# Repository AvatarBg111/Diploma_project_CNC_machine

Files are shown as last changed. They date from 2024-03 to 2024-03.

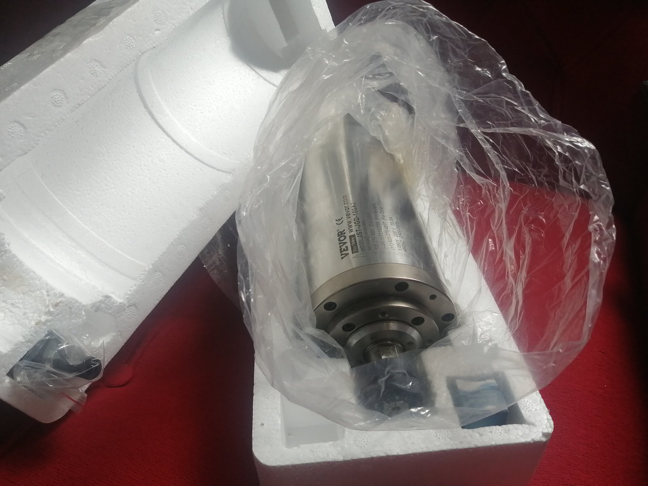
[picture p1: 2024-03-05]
Docs/Pictures/spindle_2.jpg

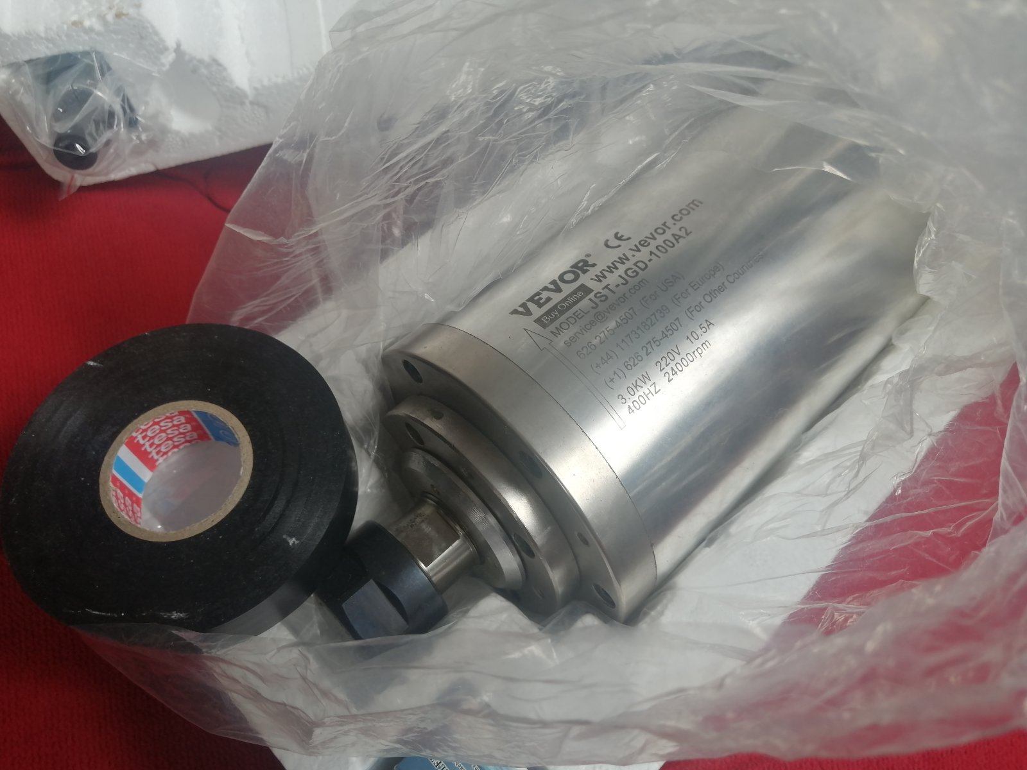
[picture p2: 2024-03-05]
Docs/Pictures/spindle_1.jpg

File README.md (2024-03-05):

# Diploma_project_CNC_machine
Repository for diploma project on the topic "System for controlling a CNC machine"

## V0.1 - 23.01.2024
 - most peripherals are configured
 - made loading screen with main menu
 - working on functionality of main and sub menus
 - working on MPG (manual pulse generator) mode

## V0.2 - 09.02.2024
 - Most menus/submenus are partially functional
 - MPG settings (for axes and spindle) are to be implemented
 - MPG mode is partially functional

## V0.3 - 19.02.2024
 - Main functionalities are complete

## V1.0 - 05.03.2024
 - Basic documentation added

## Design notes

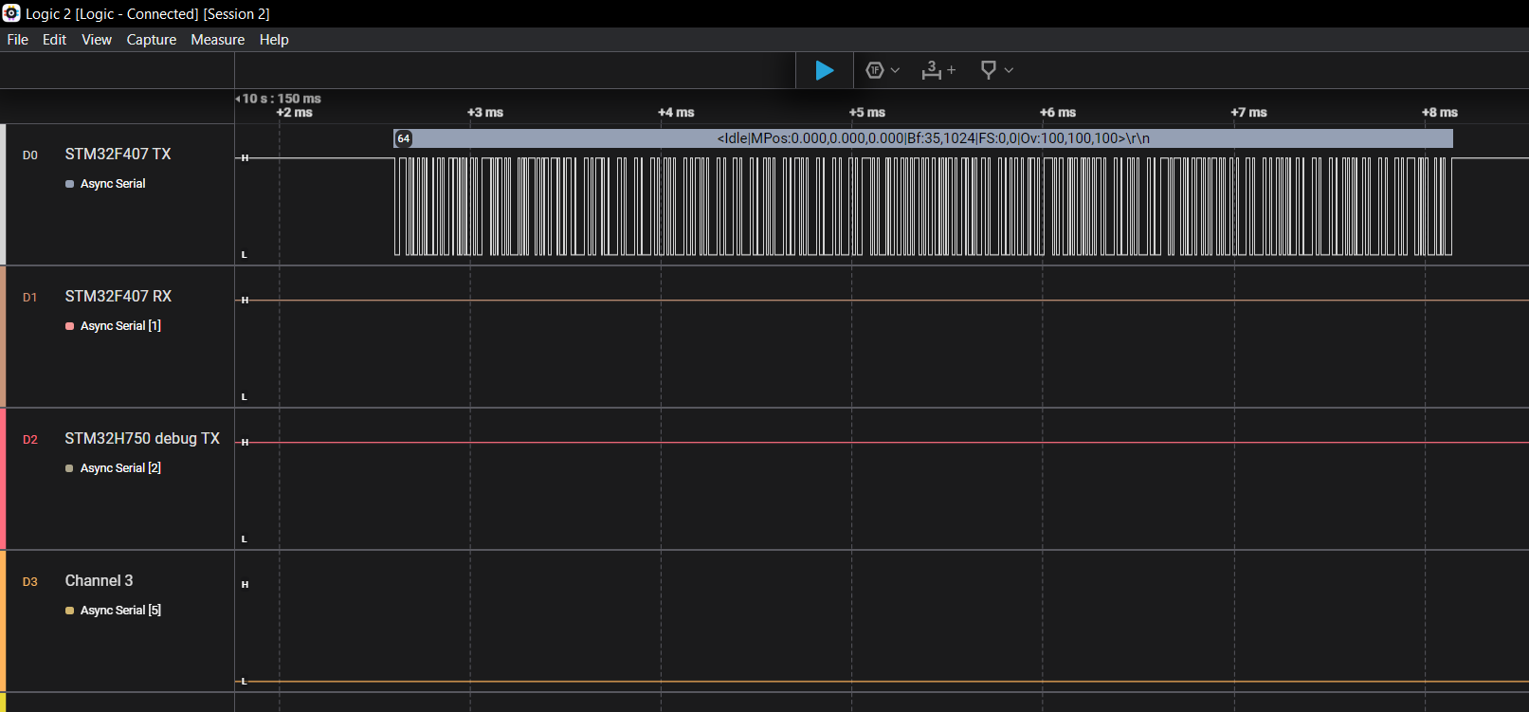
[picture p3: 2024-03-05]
Docs/Captures/grblHAL_MPG_communication_saleae_capture_6.png

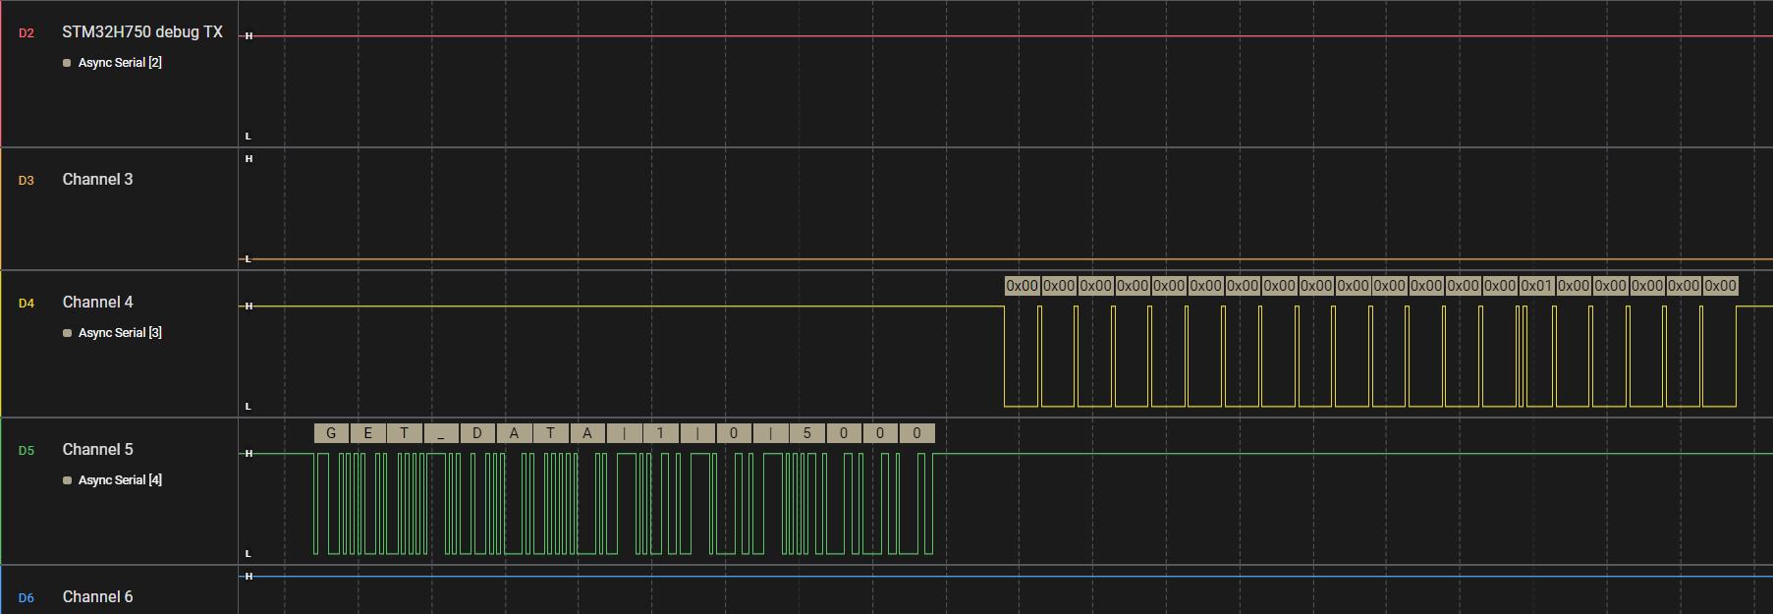
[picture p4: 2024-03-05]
Docs/Captures/pendant_communication_saleae_capture_1.png

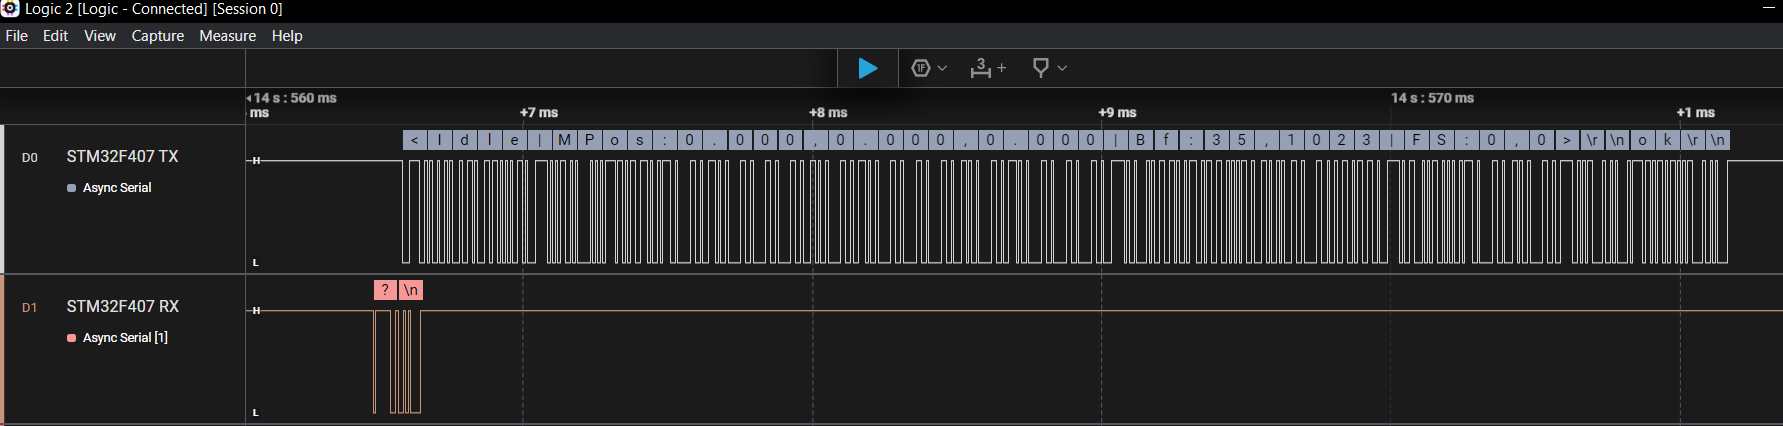
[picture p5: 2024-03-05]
Docs/Captures/grblHAL_MPG_communication_saleae_capture_1.png

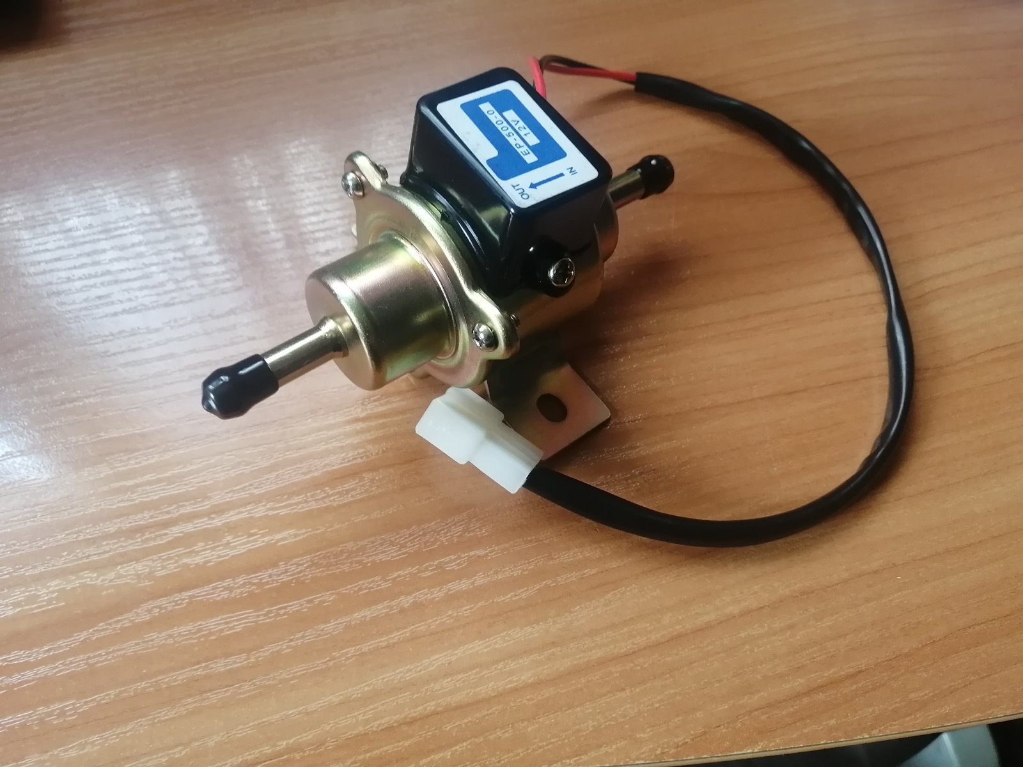
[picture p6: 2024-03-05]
Docs/Pictures/oil_pump.jpg

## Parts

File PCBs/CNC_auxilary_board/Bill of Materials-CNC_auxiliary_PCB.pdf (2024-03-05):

Value | Designator | Footprint | Quantity | Comment | Description
470μF | C1, C2, C3, C4 | CAP 8x12 | 4 | 470μF | Electrolytic capacitor, Long Life 8000h/105C, Low impedance, 470uF/ 16V 20%, 8.0x11.5mm, RM3.5mm
100nF 50V | C5, C6, C7, C8, C11, C12, C13, C15, C16, C17, C18 | SMD 0603 CAP | 11 | 100nF 50V | 100nF 50V X7R +-10%
22uF 16V | C9 | SMD 1206 CAP | 1 | 22uF 16V | 22uF 16V X5R +-20%
220μF | C10, C14 | CAP 6.3x12 | 2 | 220μF | Electrolytic capacitor, RM series, 20%,-40~105°C, 6.3x7mm RM2.5
1N4148W | D1, D2, D3, D5, D6, D7, D9, D10, D12, D13, D14, D17 | SOD123 | 12 | 1N4148W | Diode Standard 100V 300mA _DC_ Surface Mount SOD-123
SK24 | D4 | SMB | 1 | SK24 | Diode 40V 2A UFM0.55V/2A IFM 50A IR 0.45mA, Schottky
KP-2012SURCK | D8 | SMD 0805 LED-R | 1 | KP-2012SURCK | LED 2.0x1.25mm, 50-160 mcd@20mA, W.Clear, 120°
BZV55C6V8 | D11, D16 | SOD80C | 2 | BZV55C6V8 | 500 mW 5% 6.8V minimelf
BZV55C22 | D15 | SOD80C | 1 | BZV55C22 | 500 mW 5% 22V minimelf
5A | F1, F3 | FUSE HOLDER | 2 | 5A | Fuse Holder, 250 V, 6 A, Pcb Fuse Holder, Through Hole, P22,4mm
10A | F2 | FUSE HOLDER | 1 | 10A | Fuse Holder, 250 V, 6 A, Pcb Fuse Holder, Through Hole, P22,4mm
Wire | J1, J2, J3, J4, J5, J6, J7, J8, J11, J12, J13, J14, J15, J16, J17, J18, J19, J20, J21, J22, J23, J24, J27, J28, J30, J31 | Wire-2 | 26 | +12V, Water pump +, GND, Water pump -, +12V_OUT, Oil pump +, Oil pump -, +48V X, +48V X OUT, button STOP, +48V Y, +48V Y OUT, +48V Z, +48V Z OUT, Coil A+, Coil B+, Coil A-, Coil B-, High Voltage A-, High Voltage B-, Water sensor, Oil sensor | Wire
PN1X7 | J9 | PN1X7 | 1 | PN1X7 | Single Row / Straight / Without Shroud Female header Female 7 | WÃ¼rth Elektronik 61300711821 @ Pin header, socket _Si...
PN1X8 | J10 | PN1X8 | 1 | PN1X8 | Single Row / Straight / Without Shroud Female header Female 8 | WÃ¼rth Elektronik 61300711821 @ Pin header, socket _Si...
PN1X2 | J25, J26, J29, J32, J33, J34, J35 | PN1X2 | 7 | X limit switch, Y limit switch, Z limit switch, Probe switch, Hold button, Start button, Door switch | Single Row / Straight / Without Shroud Female header Female 2@ Pin header, socket _Si...
RAS-12-15 | K1, K2, K3, K4, K5, K6, K7 | RELAY RAS-12-15 (SPDT) | 7 | RAS-12-15 | RELAY 12V /30mA 15A/ 24VDC(120VAC) 10A/ 250VAC
CL220uH | L1, L2 | INDC RBQE | 2 | CL220uH | Toroidal Coil 220uH 0.099 ohm 3000mA 20%
CL1.0mH | L3 | DRH104R | 1 | CL1.0mH | CL1.0mH SDI104R (DRH104R); 2.959 ohm, 0.48A, 20%
DTC114YKA | Q1, Q3, Q5, Q6, Q9, Q13, Q18, Q20, Q21, Q22, Q23, Q25, Q27, Q28, Q29, Q30 | SOT-346 (SC59) Black | 16 | DTC114YKA | NPN Digital 50V 100mA 200mW R1=10kOm R2=47kOm
AP2306GN | Q2, Q4, Q7, Q10, Q11, Q14, Q15, Q16 | SOT-23-3 | 8 | AP2306GN | NMOS 20V 5.3A 1.38W 35mOhm/4.5V; 50mOhm/2.5V
SST2222A | Q8, Q12, Q19, Q26 | SOT-23-3 | 4 | SST2222A | Transistor NPN 40V 600mA 300MHz 350mW
BC807-25 | Q17, Q24 | SOT-23-3 | 2 | BC807-25 | Transistor PNP 45V 500mA 0.25W HFE 160-400
22k | R1, R3, R4, R6, R8, R9, R11, R12, R14, R16, R17, R18, R19, R20, R22, R23, R29, R30, R31, R33, R34, R37, R38, R39, R41, R42 | SMD 0603 | 26 | 22k | RES
47k | R2, R5, R10, R15, R21, R24, R26, R28 | SMD 0603 | 8 | 47k | RES
10k | R7 | SMD 0603 | 1 | 10k | RES
2,4k | R13, R27, R36 | SMD 0603 | 3 | 2,4k | RES
220k | R25, R35 | SMD 0603 | 2 | 220k | RES
15k | R32, R40 | SMD 0603 | 2 | 15k | RES
SMBJ13A | TZ1 | DO-214AA (SMB) | 1 | SMBJ13A | Transient Voltage Suppressors, Uni-directional, 600W, UBRmin14.4V@1mA

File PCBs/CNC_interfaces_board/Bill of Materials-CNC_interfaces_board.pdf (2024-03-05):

Value | Designator | Footprint | Quantity | Comment | Description
680μF | C1 | CAP 10x16 | 1 | 680μF | Electrolytic capacitor, TM series, 20%,-55~105°C, 10x16mm RM5, 0.1Ohm
10uF | C2 | SMD 1210 CAP | 1 | 10uF | C1210 10uF 35V X7R
220uF | C3 | SMD 7343-43 | 1 | 220uF | Cap Tant Solid 220uF 10V E CASE 10% _7.3 X 4.3 X 4mm_ SMD 7343-43 0.1 Ohm 125В °C T/R
100nF 50V | C4 | SMD 0603 CAP | 1 | 100nF 50V | 100nF 50V X7R +-10%
100uF | C5 | SMD 1210 CAP | 1 | 100uF | 100uF 10V X5R +-20%
1N4148W-7-F | D1, D2, D3 | SOD123 | 3 | 1N4148W-7-F | Diode Standard 100V 300mA _DC_ Surface Mount SOD-123
KP-2012 | D4, D5, D6, D7 | SMD 0805 LED-Y | 4 | KP-2012 WHITE, KP-2012 GREEN, KP-2012 ORANGE, KP-2012 RED | LED 2.0x1.25mm, 50-160 mcd@20mA, W.Clear, 120°
LQH32CN471K23L | FB1 | SMD 1210 LQH | 1 | LQH32CN471K23L | 470uH 19Ohm 60mA 10% 47uH 1.3Ohm 170mA 10%
Wire | J1, J2 | Wire-2 | 2 | +12V, GND | Wire
FPC-40PinConnector | J3 | 687140149022 | 1 | FPC-40PinConnector | 40 Position FFC, FPC Connector Contacts, Bottom 0.020 (0.50mm) Surface Mount, Right Angle
PN1X8 | J4, J8, J10, J11 | PN1X8 | 4 | PN1X8 | Single Row / Straight / Without Shroud Female header Female 8 | WÃ¼rth Elektronik 61300711821 @ Pin header, socket _Si...
PN1X4 | J5, J9 | PN1X4 | 2 | PN1X4 | Single Row / Straight / Without Shroud Female header Female 4 @ Pin header, socket _Si...
PN1X7 | J6 | PN1X7 | 1 | PN1X7 | Single Row / Straight / Without Shroud Female header Female 7 | WÃ¼rth Elektronik 61300711821 @ Pin header, socket _Si...
FPC-6PinConnector | J7 | 687106149022 | 1 | FPC-6PinConnector | 6 Position FFC, FPC Connector Contacts, Bottom 0.020 (0.50mm) Surface Mount, Right Angle
Buzzer | LS1 | XDCR_KSSG13J12-N | 1 | Buzzer
LTV356T | OPT1, OPT2 | MINI-FLAT-4 | 2 | LTV356T | Optoisolator Transistor Output 3750Vrms 1 Channel 4-SOP
DTC114YKA | Q1, Q4, Q5, Q6, Q7, Q8, Q9, Q10, Q11, Q12, Q13, Q14, Q15, Q16, Q17, Q18, Q19, Q20, Q21, Q22, Q24 | SOT-346 (SC59) Black | 21 | DTC114YKA | NPN Digital 50V 100mA 200mW R1=10kOm R2=47kOm
SST2222A | Q2, Q3, Q23 | SOT-23-3 | 3 | SST2222A | Transistor NPN 40V 600mA 300MHz 350mW
10k | R1, R2, R3, R4, R5, R6, R7, R8, R9, R10, R11, R12, R13, R14, R21, R24, R26, R27, R29, R31, R33, R35, R37, R39, R40, R41, R42, R43, R44, R45, R46, R47, R48, R49, R50, R51 | SMD 0805 | 36 | 10k | RES
220Ohm | R15, R16, R17, R18 | SMD 0805 | 4 | 220Ohm | RES
2,7k | R19, R20, R22, R23, R25, R28, R30, R32, R34, R36, R38 | SMD 0805 | 11 | 2,7k | RES
1k | R52 | SMD 0805 | 1 | 1k | RES
Button | SW1, SW2, SW3, SW4, SW5, SW6 | SW_KSR221GLFS | 6 | Button | Tactile Switch 2p SPST-NO 50mA/32V 6x3.8x2.5mm
STM32H750VBT6 WeActStudio | U1 | WeActStudio STM32H750VBT6 | 1 | STM32H750VBT6 WeActStudio | Board
STM32F407VGT6 DevEBox | U2 | DevEBox V3.0 STM32F407VGT6 | 1 | STM32F407VGT6 DevEBox | Board
BA05CC0WFP-E2 | U3 | DPAK228P968X238-4N | 1 | BA05CC0WFP-E2 | LDO Regulator

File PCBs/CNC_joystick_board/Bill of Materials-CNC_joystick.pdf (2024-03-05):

Value | Designator | Footprint | Quantity | Comment | Description
470μF | C1 | CAP 8x12 | 1 | 470μF
22uF | C2 | YelloW SMD 1210 CAP TANT | 1 | =+'22uF'+' '+'16V' | TANT B SMD 22uF 16V 293D226X9016B2TE3
100nF 50V | C3, C5, C6, C7, C8, C9, C10 | SMD 0603 CAP | 7 | 100nF 50V | CL10B104KB85PNC
10uF | C4 | Yellow SMD 1206 CAP TANT | 1 | =+'10uF'+' '+'10V' | TANT A SMD 10uF 10V TAJA106K010RNJ
ZLLS1000TA | D1 | SOT-23-3 | 1 | ZLLS1000TA | Schottky Diode, Vr=40V, If=1.16A, Uf=0.43V/1.0A, Ifsm=22A/<100us, Ir=5uA typ, trr=5.0ns typ
OSY5LU3133A | D2, D3, D4, D5, D6, D7 | LED-3mm Y | 6 | OSY5LU3133A | LED 3mm, 80mcd@20mA, 590nm Yellow, Transparent, 30°
OSR6NU3134A | D8, D9, D10, D11 | LED-3mm R | 4 | OSR6NU3134A | 3mm, 20mcd@30mA, 640nm Hi-Eff Red, Diffused, 30°
MF-NSMF035X-2 | F1 | SMD 1206 FUSE | 1 | MF-NSMF035X-2 | PTC Resettable Fuse, Ihold 0.35A, 16V, SMD 1206
Wire | J1, J2, J3, J4 | PN1X4, Wire-2 | 4 | PN1X4, p1, p2 | Single Row / Straight / Without Shroud Female header Female 4 @ Pin header, socket _Si..., Wire
CL1.0mH | L1 | DRH104R | 1 | CL1.0mH | CL1.0mH SDI104R (DRH104R); 2.959 ohm, 0.48A, 20%
1k | R1, R4 | SMD 0603 | 2 | 1k | RES
100k | R2, R3 | SMD 0603 | 2 | 100k | RES
270R | R5, R6, R7, R8, R9, R10, R11, R12, R18, R19 | SMD 0603 | 10 | 270R | RES
180R | R13, R14, R15, R16, R17 | SMD 0603 | 5 | 180R | RES
encoder | SW1, SW2 | PN1X4 | 2 | encoder | Handwheel CNC Pulser, Rotary Encoder, 60mm, 100PPR, 5V, 4Pin, <=120mAq Silver
Switch 3 Pos | SW3, SW4, SW11, SW12 | PN1X8 | 4 | Switch 3 Pos | Latching, 22mm, 5V, 8Pin, Silver, Blue led
Switch 2 Pos | SW5 | PN1X4 | 1 | Switch 2 Pos | Latching, 16mm, 5V, 3Pin, Silver
Button 1 LED | SW6, SW7, SW8, SW9, SW10 | PN1X4 | 5 | Button 1 LED | Momentary, 22mm, 5V, 4Pin, Silver, Led
SMBJ13A | TZ1 | DO-214AA (SMB) | 1 | SMBJ13A | Transient Voltage Suppressors, Uni-directional, 600W, UBRmin14.4V@1mA
MCP1703T-3302E | U1 | SOT-89(MB) | 1 | MCP1703T-3302E | 3.3V±2% 250mA, LDO 0.725V, Vinmax=16V, linear voltage regulator
STM32F103C8T6 | U2 | QFP50P900X900X160-48N | 1 | STM32F103C8T6 | ARMÂ® CortexÂ®-M3 STM32F1 Microcontroller IC 32-Bit 72MHz 64KB (64K x 8) FLASH 48-LQFP (7x7)

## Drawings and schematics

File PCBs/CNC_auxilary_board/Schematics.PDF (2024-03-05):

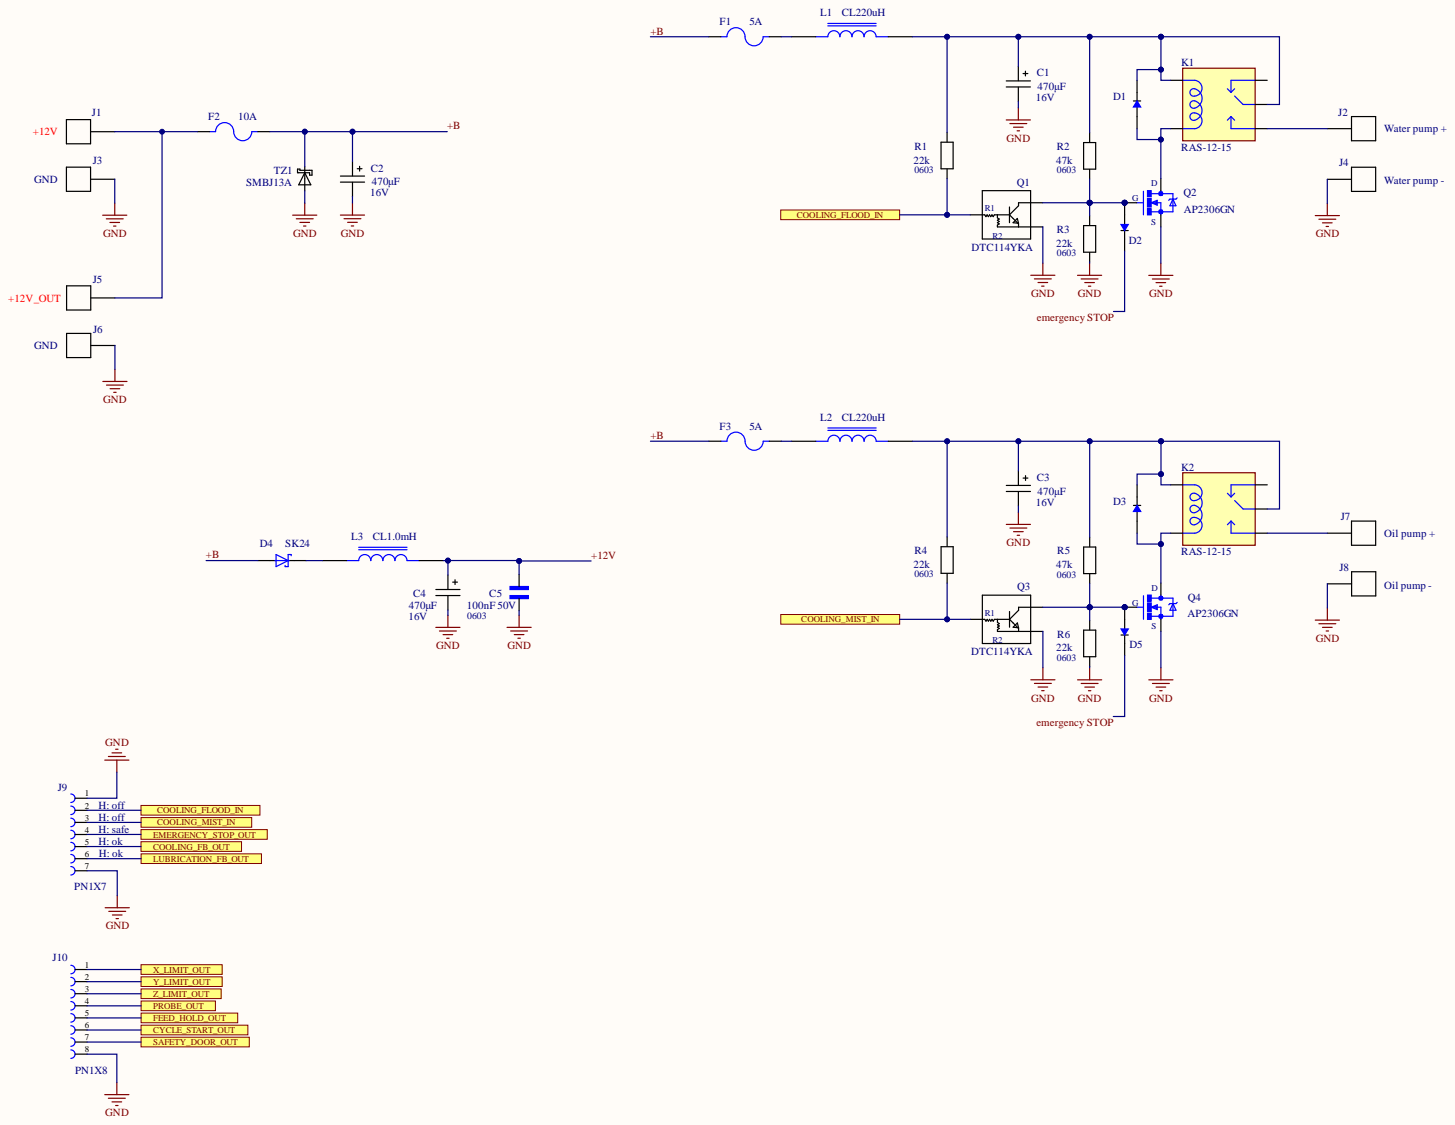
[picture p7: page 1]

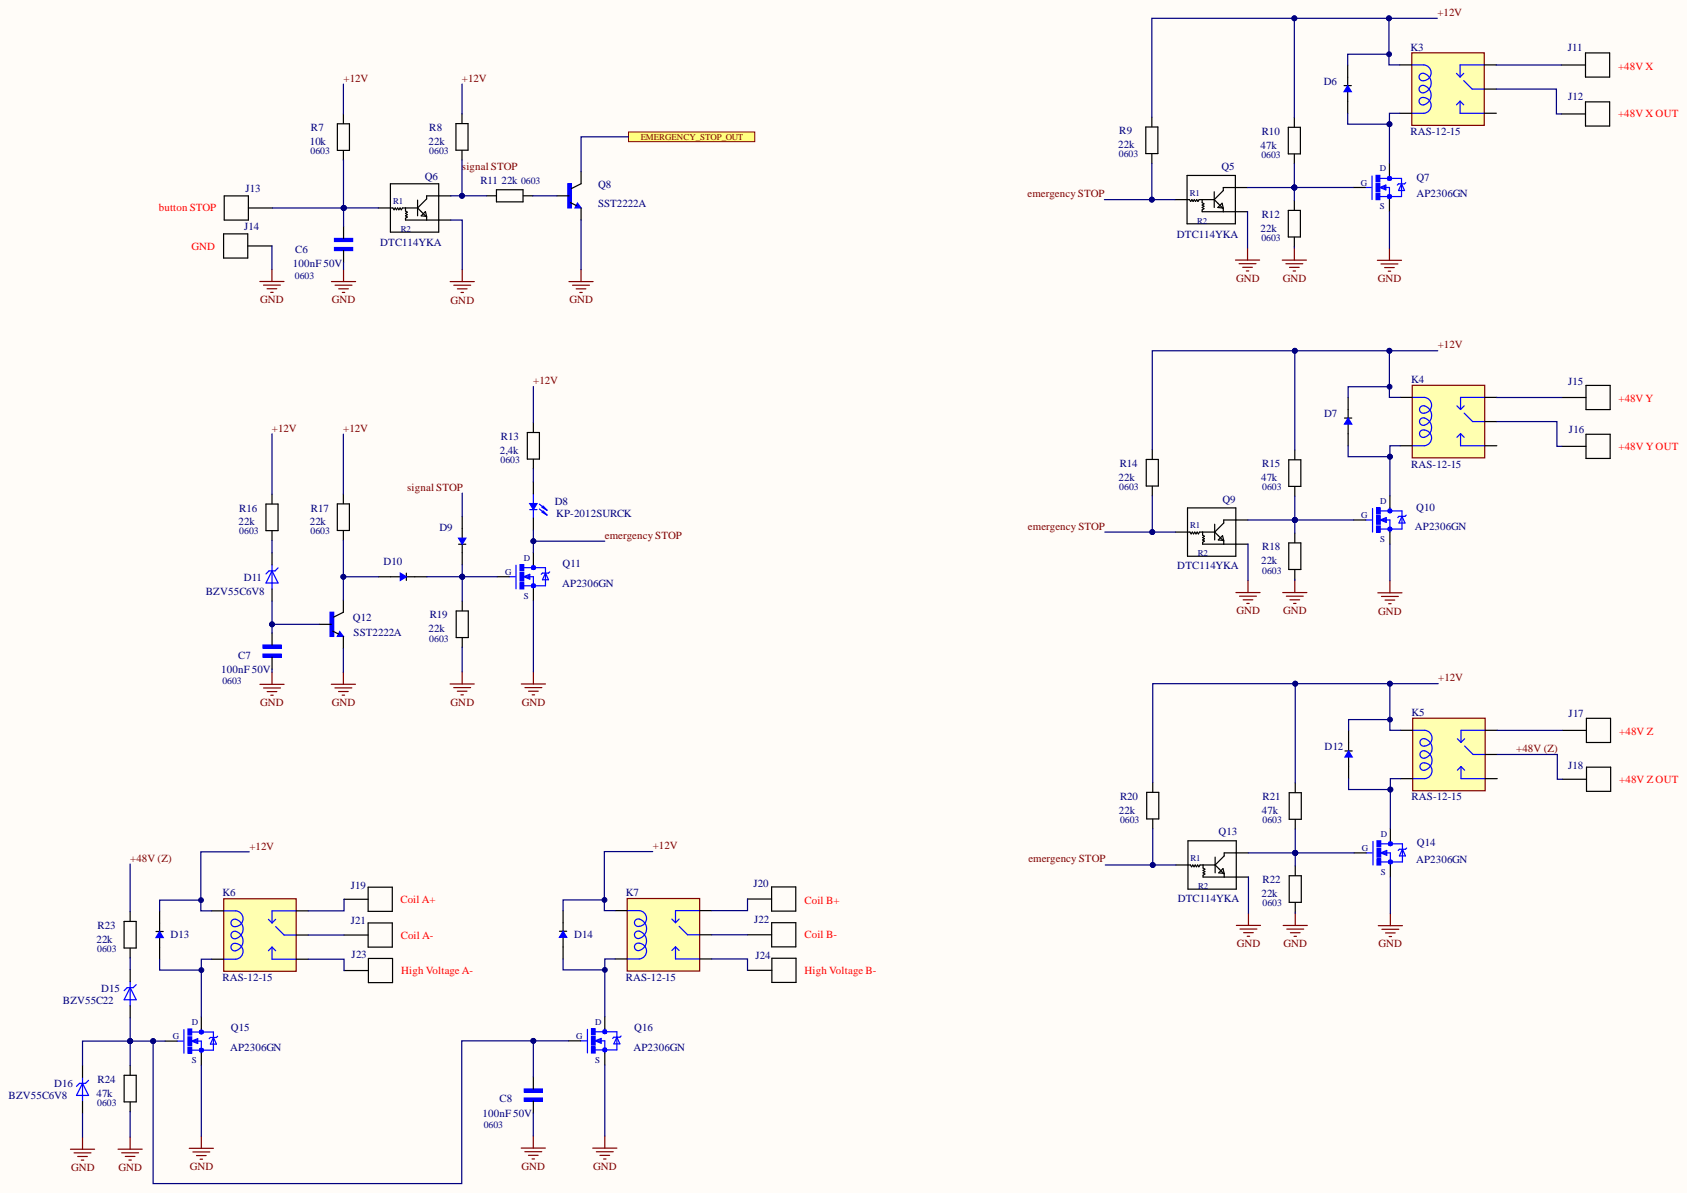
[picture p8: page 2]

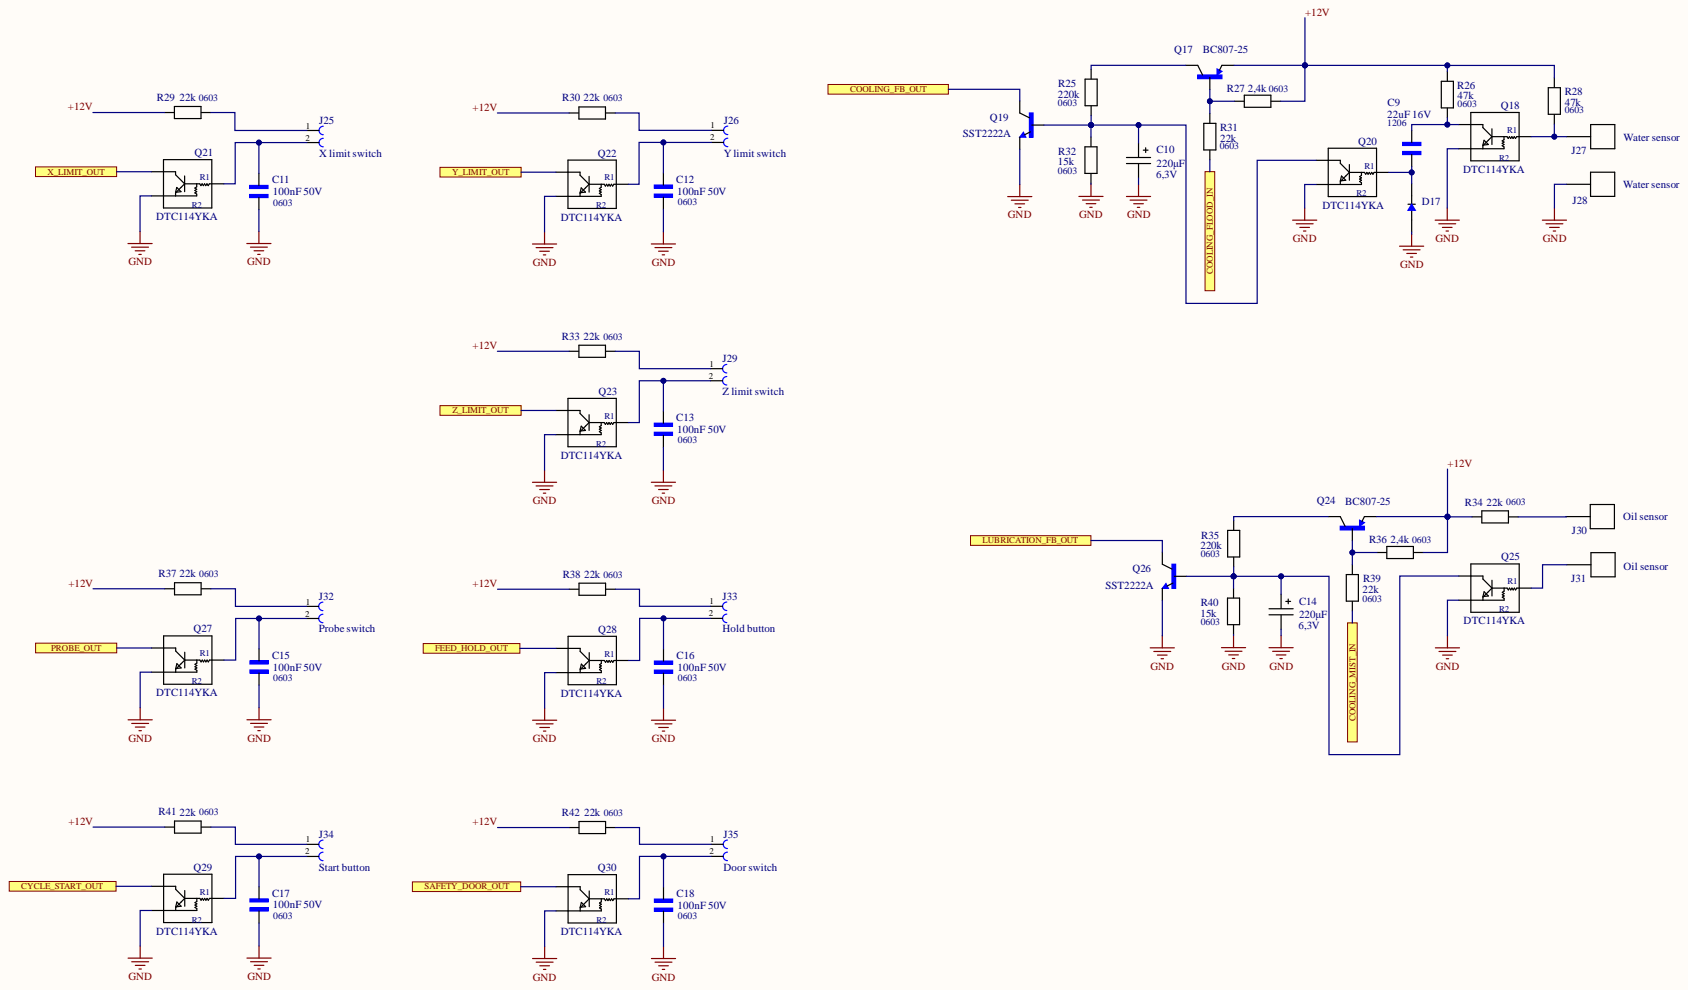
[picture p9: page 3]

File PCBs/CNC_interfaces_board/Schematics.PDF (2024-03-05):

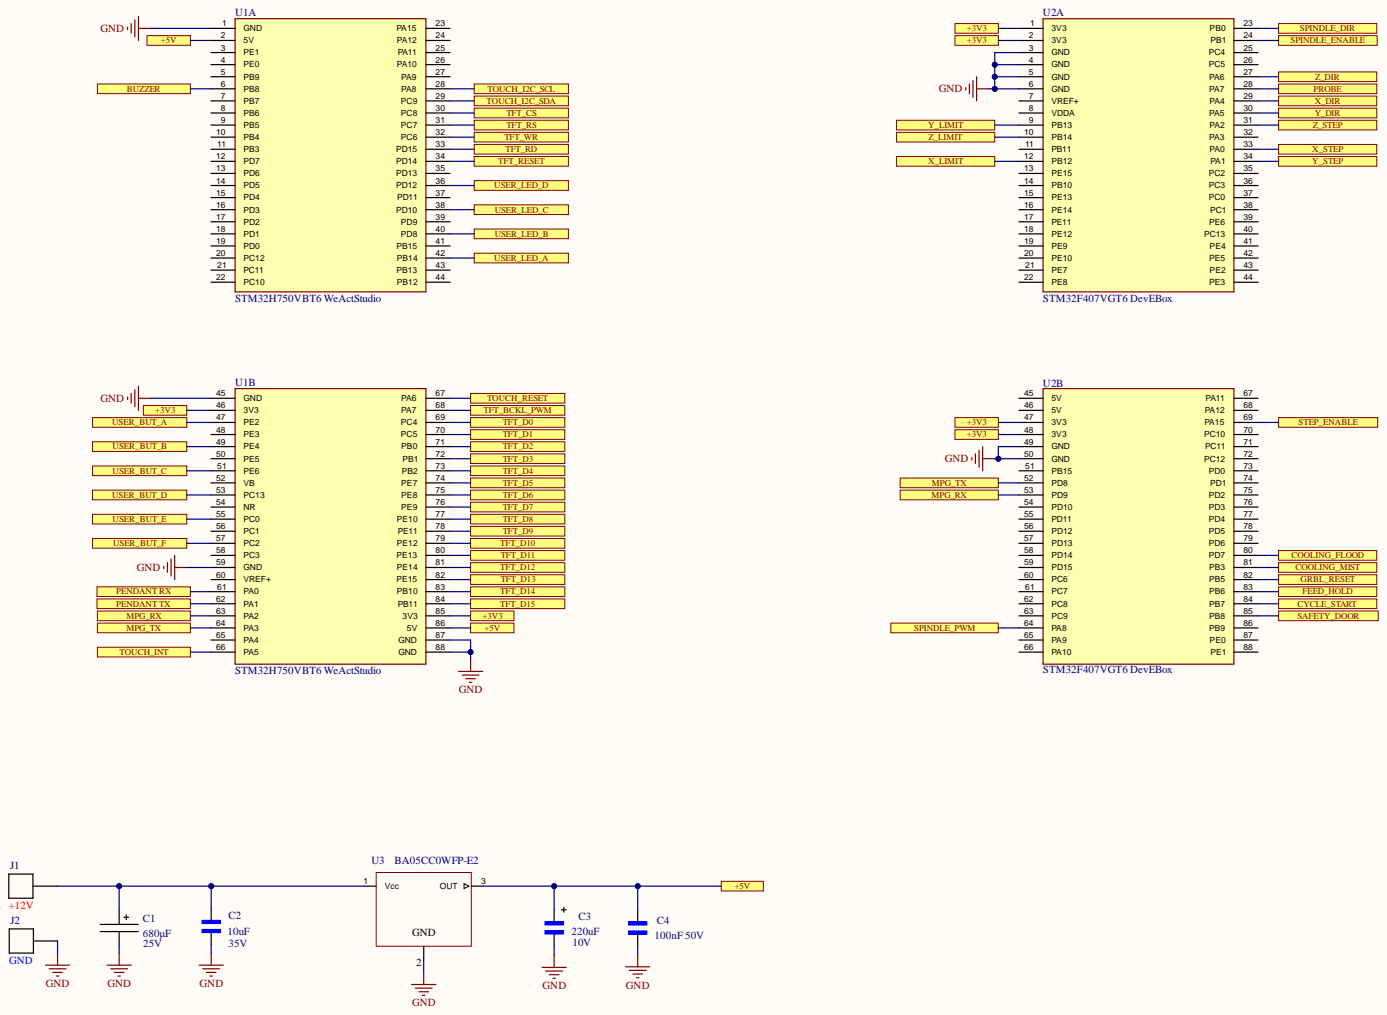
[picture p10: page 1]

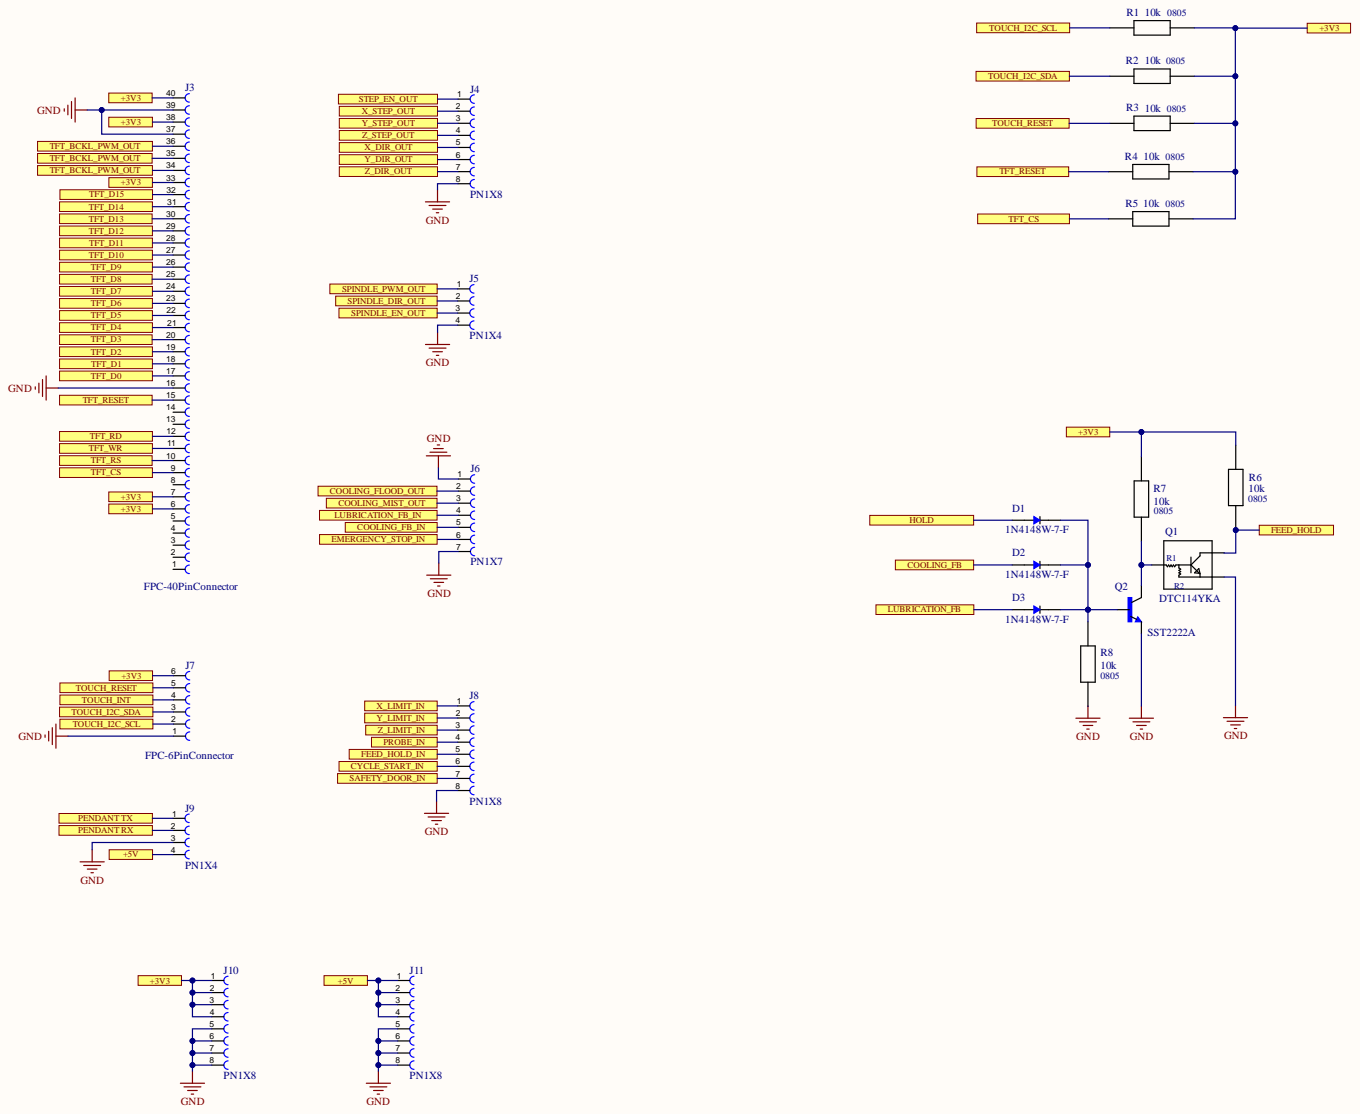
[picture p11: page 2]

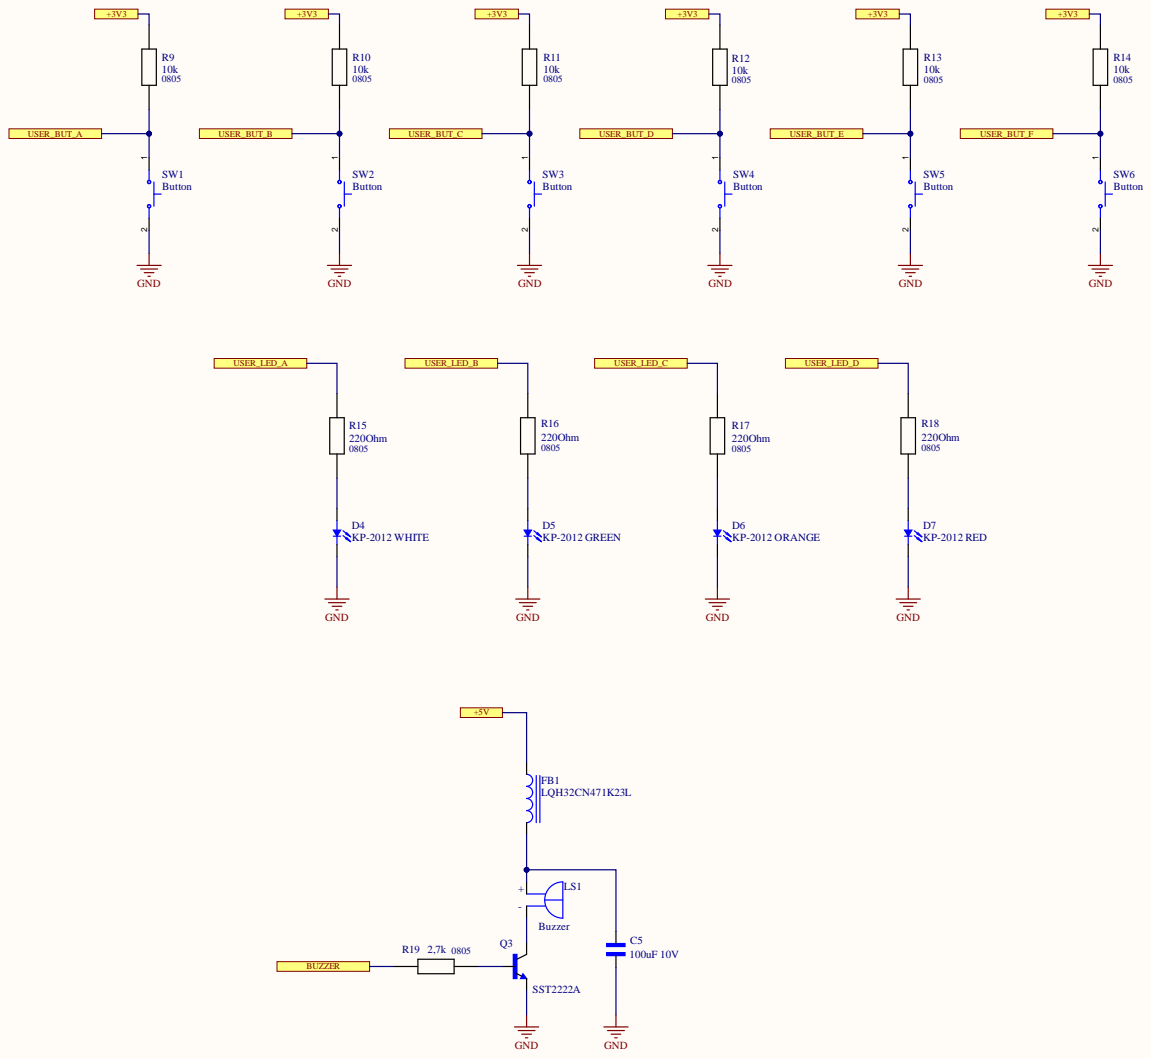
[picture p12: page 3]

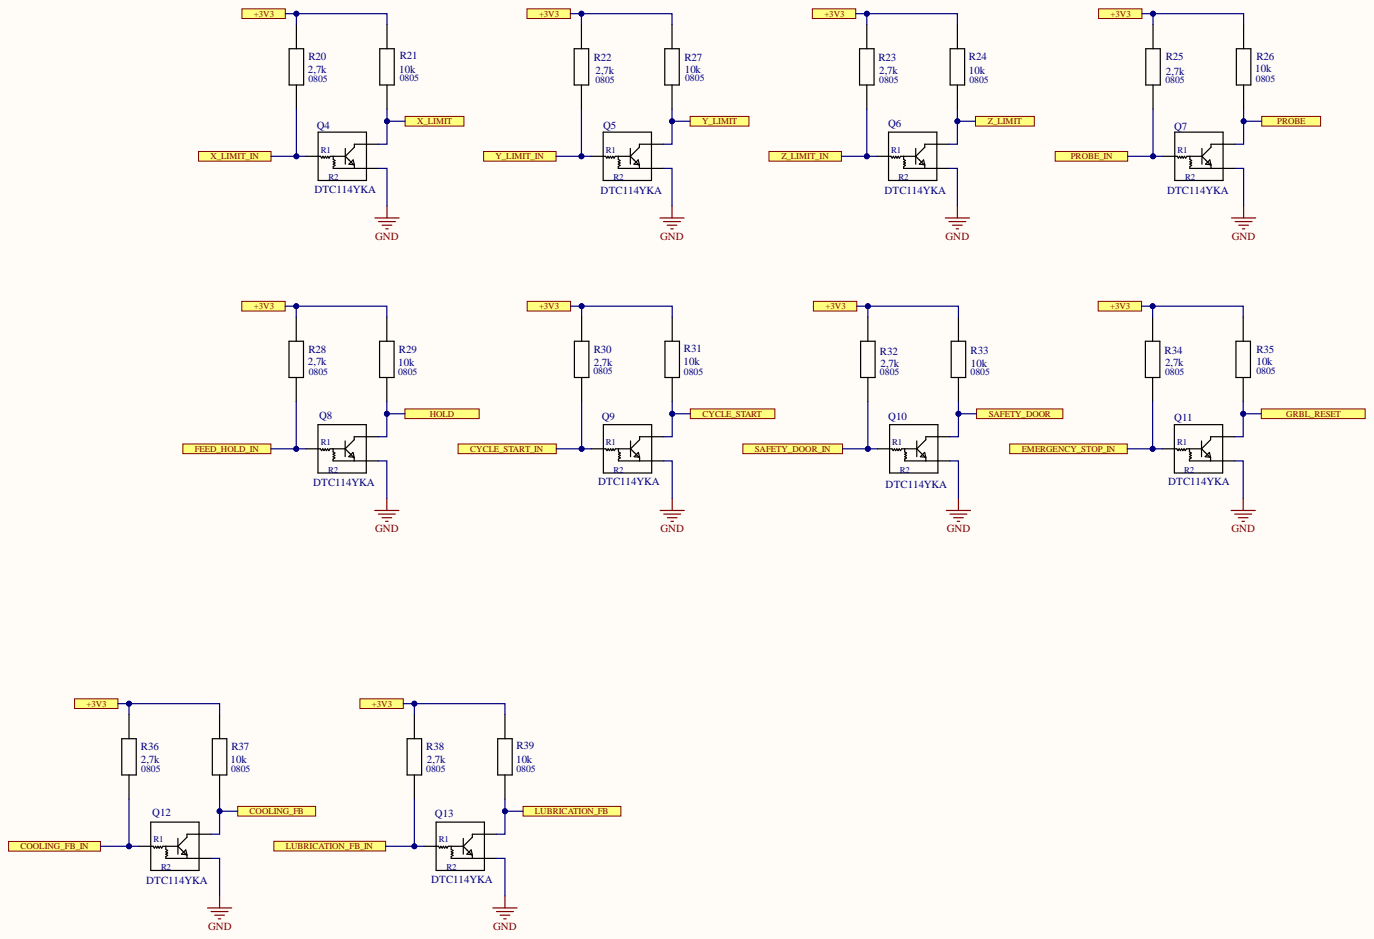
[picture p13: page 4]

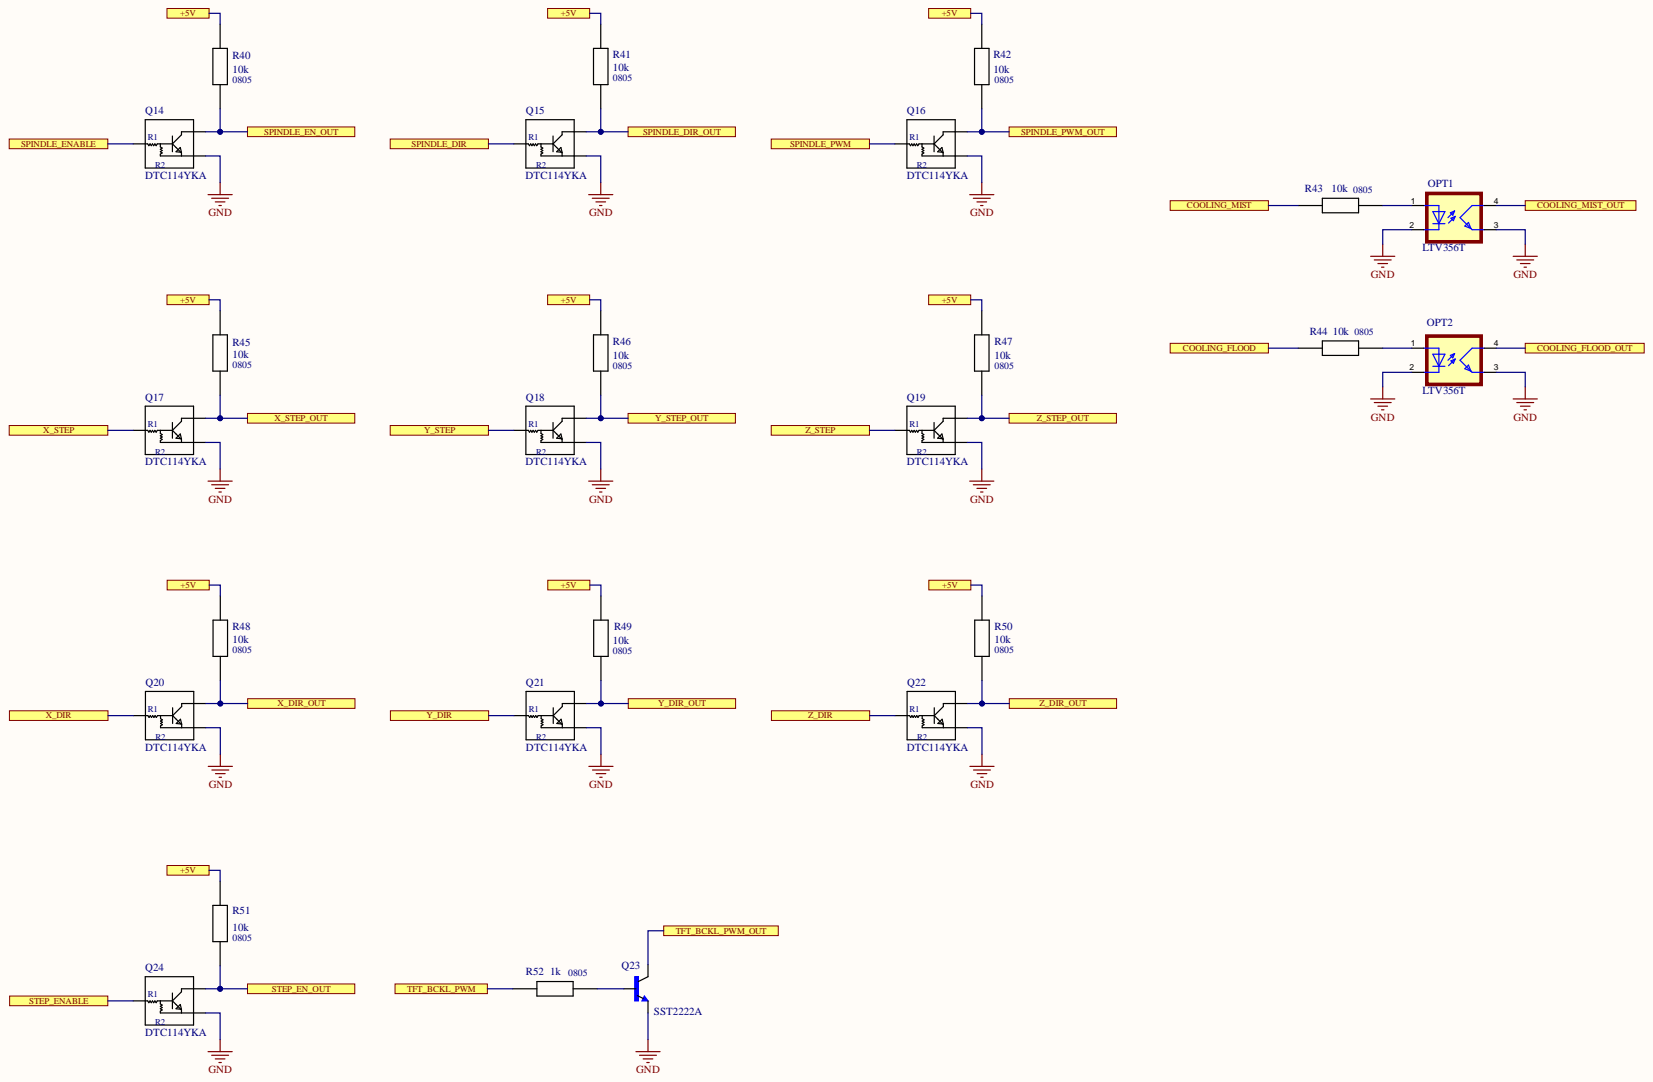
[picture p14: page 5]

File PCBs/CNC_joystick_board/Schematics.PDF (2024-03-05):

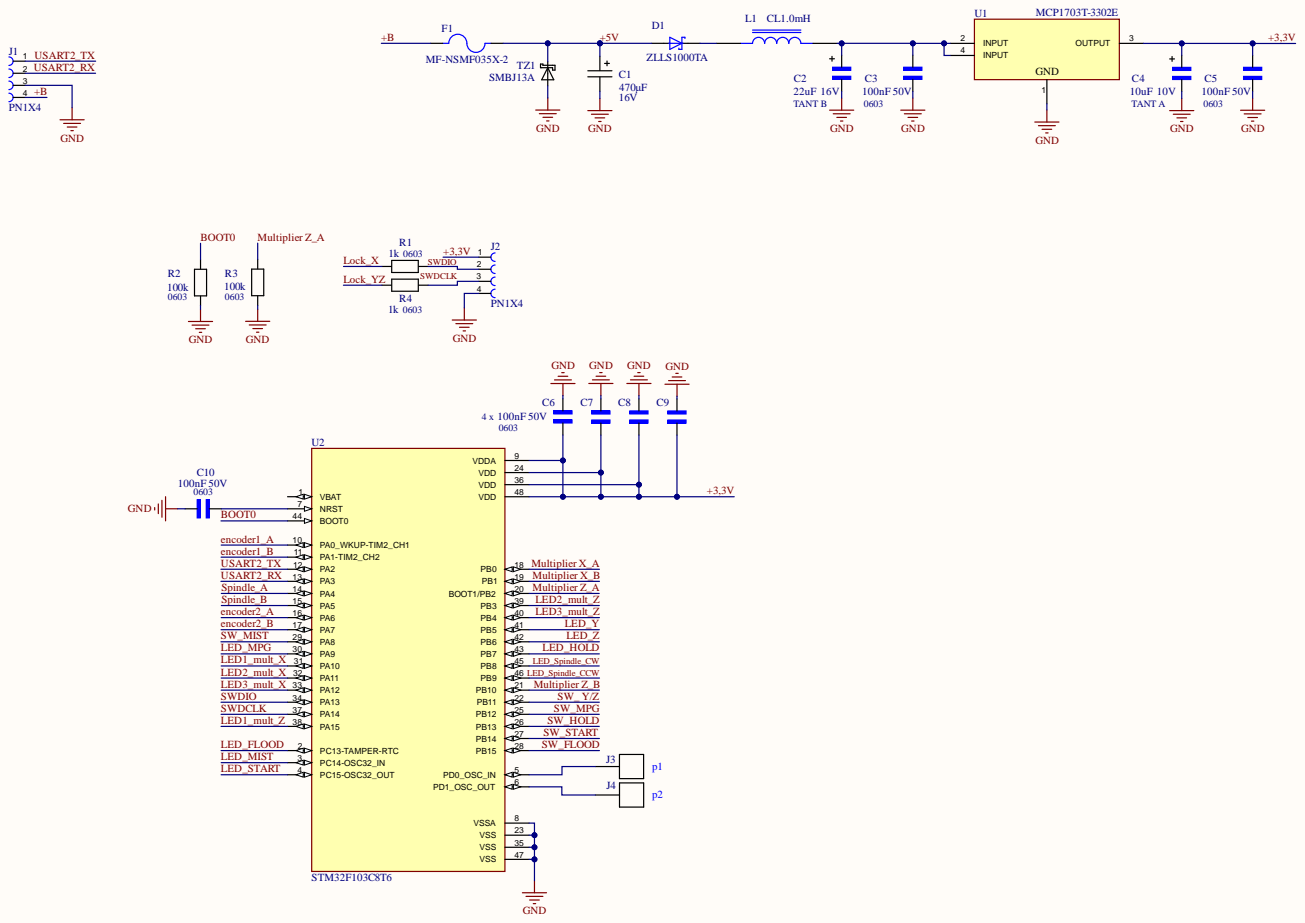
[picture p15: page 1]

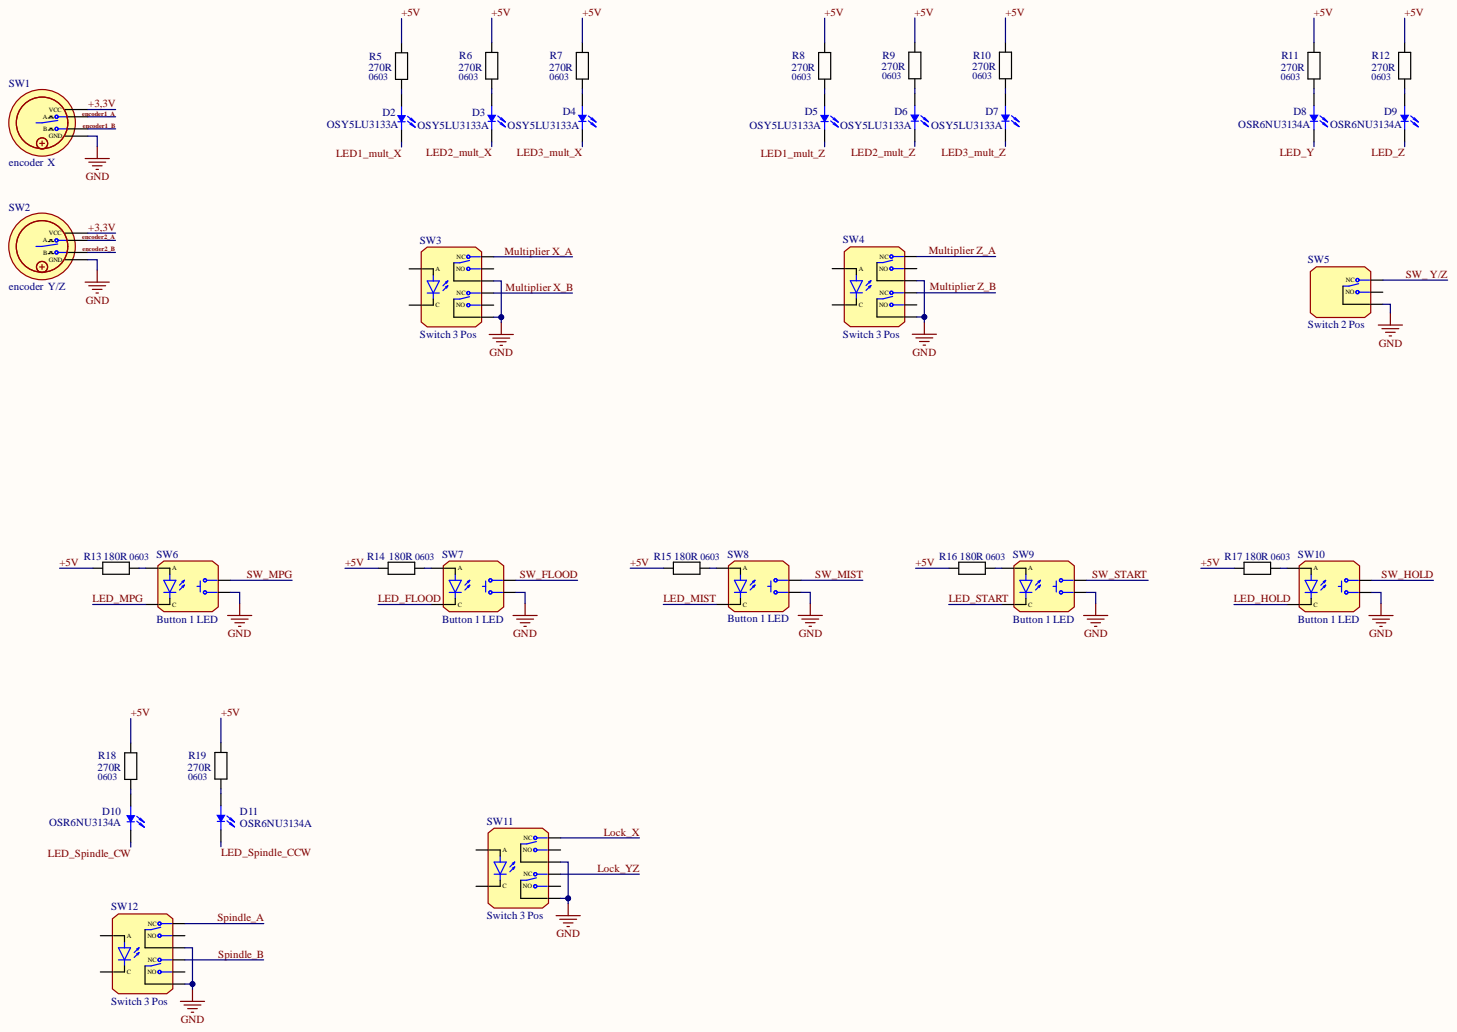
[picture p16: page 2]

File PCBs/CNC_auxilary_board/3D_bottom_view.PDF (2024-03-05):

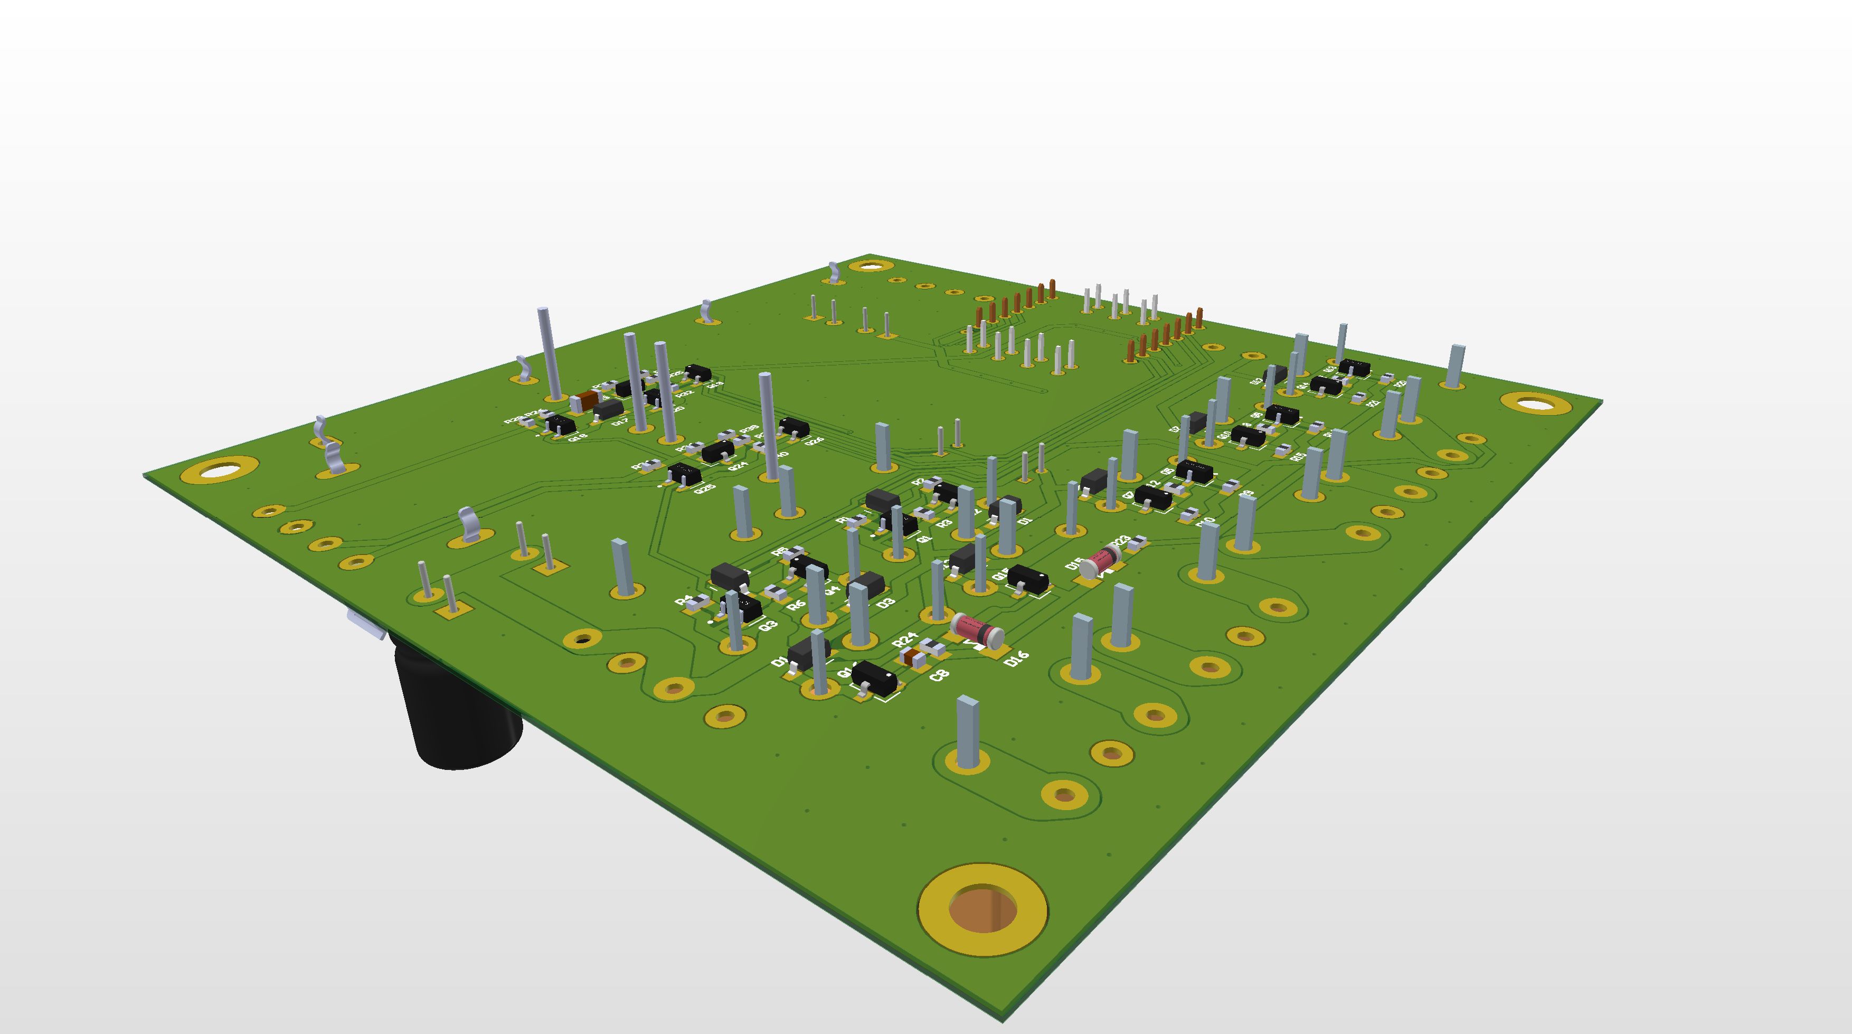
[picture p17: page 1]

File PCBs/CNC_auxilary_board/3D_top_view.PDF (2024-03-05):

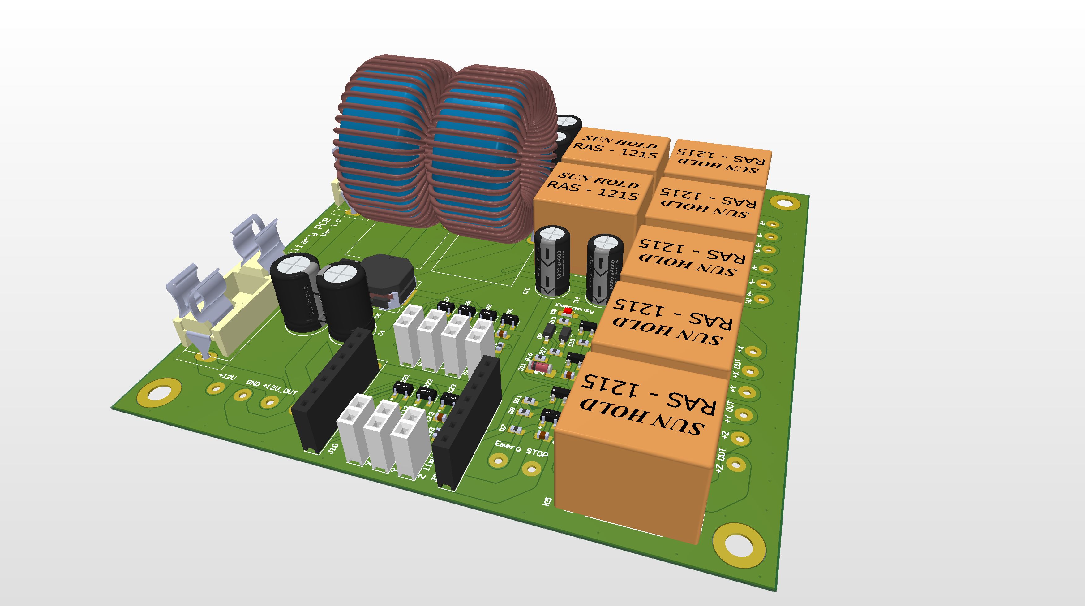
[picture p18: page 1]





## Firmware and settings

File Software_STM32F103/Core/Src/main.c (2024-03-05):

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
/* Includes ------------------------------------------------------------------*/
#include "main.h"

/* USER CODE BEGIN Includes */
#include "buttons.h"
#include "uart_comm.h"
#include "stm32f1xx_it.h"

/* USER CODE END Includes */

/* USER CODE BEGIN PD */
#define Y_OR_Z_BUT_DELAY_CH 0
#define MPG_BUT_DELAY_CH 1
#define FLOOD_BUT_DELAY_CH 2
#define MIST_BUT_DELAY_CH 3

/* USER CODE END PD */

TIM_HandleTypeDef htim2;
TIM_HandleTypeDef htim3;
TIM_HandleTypeDef htim4;

UART_HandleTypeDef huart2;
DMA_HandleTypeDef hdma_usart2_rx;
DMA_HandleTypeDef hdma_usart2_tx;

/* USER CODE BEGIN PV */
bool process_inputs_flag = false;
bool pendant_status = false;
uint8_t pendant_mpg_status = MPG_STATUS_DISABLED;

uint8_t button_action_delay_cnt_ch[16] = {0};
const uint8_t button_delay_action_cnt = BUTTON_DELAY_ACTION_TIME / PROCESS_INPUTS_DELAY;

/* USER CODE END PV */

void SystemClock_Config(void);
static void MX_GPIO_Init(void);
static void MX_DMA_Init(void);
static void MX_TIM2_Init(void);
static void MX_TIM3_Init(void);
static void MX_USART2_UART_Init(void);
static void MX_TIM4_Init(void);
/* USER CODE BEGIN PFP */
void Init_interfaces(void);
void turn_off_leds(void);
void process_inputs(void);
uint8_t get_spindle_mode(void);
uint8_t get_x_axis_multiplier(void);
uint8_t get_yz_axis_multiplier(void);

/* USER CODE END PFP */

/* USER CODE BEGIN 0 */
#define ENCODER_1_TIM htim2
#define ENCODER_2_TIM htim3

extern pendant_data_t pendant_data;

/* USER CODE END 0 */

/**
  * @brief  The application entry point.
  * @retval int
  */
int main(void)
{
  /* MCU Configuration--------------------------------------------------------*/

  /* Reset of all peripherals, Initializes the Flash interface and the Systick. */
  HAL_Init();

  /* Configure the system clock */
  SystemClock_Config();

  /* Initialize all configured peripherals */
  MX_GPIO_Init();
  MX_DMA_Init();
  MX_TIM2_Init();
  MX_TIM3_Init();
  MX_USART2_UART_Init();
  MX_TIM4_Init();
  /* USER CODE BEGIN 2 */
  // Initialize interfaces
  Init_interfaces();

  /* USER CODE END 2 */

  /* Infinite loop */
  /* USER CODE BEGIN WHILE */
  while(1)
  {
	// The program will enter this if statement when the flag
	// has been set which happens inside TIM4 interrupt handler
	if(process_inputs_flag && pendant_status){
		// Call function for processing system inputs
		process_inputs();

		// Reset the entry flag
		process_inputs_flag = false;
	}
    /* USER CODE END WHILE */

    /* USER CODE BEGIN 3 */
  }
  /* USER CODE END 3 */
}

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
/* USER CODE BEGIN 4 */
/**
  * @brief Initialize interfaces
  */
void Init_interfaces(void){
	// Start encoder timers
	HAL_TIM_Encoder_Start(&htim2, TIM_CHANNEL_ALL);
	HAL_TIM_Encoder_Start(&htim3, TIM_CHANNEL_ALL);

	// Start TIM4 for button de-bouncer
	HAL_TIM_Base_Start_IT(&htim4);

	// Assign buttons/switches a de-bouncer channel
	set_button_channel(SPINDLE_MODE_SW_NC_1_GPIO_Port, SPINDLE_MODE_SW_NC_1_Pin, SPINDLE_3POS_SW_NC_1_CH);
	set_button_channel(SPINDLE_MODE_SW_NC_2_GPIO_Port, SPINDLE_MODE_SW_NC_2_Pin, SPINDLE_3POS_SW_NC_2_CH);
	set_button_channel(AXIS_X_MULTIPLIER_SW_NC_1_GPIO_Port, AXIS_X_MULTIPLIER_SW_NC_1_Pin, AXIS_X_MULTIPLIER_SW_NC_1_CH);
	set_button_channel(AXIS_X_MULTIPLIER_SW_NC_2_GPIO_Port, AXIS_X_MULTIPLIER_SW_NC_2_Pin, AXIS_X_MULTIPLIER_SW_NC_2_CH);
	set_button_channel(AXIS_YZ_MULTIPLIER_SW_NC_1_GPIO_Port, AXIS_YZ_MULTIPLIER_SW_NC_1_Pin, AXIS_YZ_MULTIPLIER_SW_NC_1_CH);
	set_button_channel(AXIS_YZ_MULTIPLIER_SW_NC_2_GPIO_Port, AXIS_YZ_MULTIPLIER_SW_NC_2_Pin, AXIS_YZ_MULTIPLIER_SW_NC_2_CH);
	set_button_channel(YZ_SW_GPIO_Port, YZ_SW_Pin, YZ_SW_CH);
	set_button_channel(MPG_SW_GPIO_Port, MPG_SW_Pin, MPG_BUT_CH);
	set_button_channel(HOLD_GPIO_Port, HOLD_Pin, HOLD_BUT_CH);
	set_button_channel(CYCLE_START_GPIO_Port, CYCLE_START_Pin, CYCLE_START_BUT_CH);
	set_button_channel(FLOOD_GPIO_Port, FLOOD_Pin, FLOOD_SW_CH);
	set_button_channel(MIST_GPIO_Port, MIST_Pin, MIST_SW_CH);
	set_button_channel(LOCK_X_AXIS_SW_GPIO_Port, LOCK_X_AXIS_SW_Pin, LOCK_X_AXIS_SW_CH);
	set_button_channel(LOCK_YZ_AXIS_SW_GPIO_Port, LOCK_YZ_AXIS_SW_Pin, LOCK_YZ_AXIS_SW_CH);

	// Turn off all LEDs
	turn_off_leds();

	// Start UART2 reception
	start_uart2_reception();
}

/**
  * @brief Turn off all system LEDs
  */
void turn_off_leds(void){
	HAL_GPIO_WritePin(FLOOD_LED_GPIO_Port, FLOOD_LED_Pin, LED_STATE_OFF);
	HAL_GPIO_WritePin(MIST_LED_GPIO_Port, MIST_LED_Pin, LED_STATE_OFF);
	HAL_GPIO_WritePin(CYCLE_START_LED_GPIO_Port, CYCLE_START_LED_Pin, LED_STATE_OFF);
	HAL_GPIO_WritePin(HOLD_LED_GPIO_Port, HOLD_LED_Pin, LED_STATE_OFF);
	HAL_GPIO_WritePin(MPG_ON_LED_GPIO_Port, MPG_ON_LED_Pin, LED_STATE_OFF);
	HAL_GPIO_WritePin(YZ_SW_LED_Y_GPIO_Port, YZ_SW_LED_Y_Pin, LED_STATE_OFF);
	HAL_GPIO_WritePin(YZ_SW_LED_Z_GPIO_Port, YZ_SW_LED_Z_Pin, LED_STATE_OFF);
	HAL_GPIO_WritePin(SPINDLE_CW_LED_GPIO_Port, SPINDLE_CW_LED_Pin, LED_STATE_OFF);
	HAL_GPIO_WritePin(SPINDLE_CCW_LED_GPIO_Port, SPINDLE_CCW_LED_Pin, LED_STATE_OFF);

	HAL_GPIO_WritePin(AXIS_X_MULTIPLIER_LED_1_GPIO_Port, AXIS_X_MULTIPLIER_LED_1_Pin, LED_STATE_OFF);
	HAL_GPIO_WritePin(AXIS_X_MULTIPLIER_LED_2_GPIO_Port, AXIS_X_MULTIPLIER_LED_2_Pin, LED_STATE_OFF);
	HAL_GPIO_WritePin(AXIS_X_MULTIPLIER_LED_3_GPIO_Port, AXIS_X_MULTIPLIER_LED_3_Pin, LED_STATE_OFF);

	HAL_GPIO_WritePin(AXIS_YZ_MULTIPLIER_LED_1_GPIO_Port, AXIS_YZ_MULTIPLIER_LED_1_Pin, LED_STATE_OFF);
	HAL_GPIO_WritePin(AXIS_YZ_MULTIPLIER_LED_2_GPIO_Port, AXIS_YZ_MULTIPLIER_LED_2_Pin, LED_STATE_OFF);
	HAL_GPIO_WritePin(AXIS_YZ_MULTIPLIER_LED_3_GPIO_Port, AXIS_YZ_MULTIPLIER_LED_3_Pin, LED_STATE_OFF);
}


/**
  * @brief Process system inputs
  */
void process_inputs(void){
	static bool y_or_z_last_state = false;
	uint8_t lock_x_axis = get_button_state(LOCK_X_AXIS_SW_CH);	// Get X axis lock state
	uint8_t lock_yz_axis = get_button_state(LOCK_YZ_AXIS_SW_CH); // Get Y/Z axes lock state

	// Check MPG functionality switch input (it disables/enables MPG functionality)
	if(get_button_state(MPG_BUT_CH) == GPIO_PIN_RESET){
		if(++button_action_delay_cnt_ch[MPG_BUT_DELAY_CH] >= button_delay_action_cnt || \
		   button_action_delay_cnt_ch[MPG_BUT_DELAY_CH] == 1){
			if(button_action_delay_cnt_ch[MPG_BUT_DELAY_CH] != 1 && button_delay_action_cnt != 1){
				button_action_delay_cnt_ch[MPG_BUT_DELAY_CH] = 0;
			}

			if(pendant_mpg_status != MPG_STATUS_DISABLED){
				pendant_mpg_status = MPG_STATUS_DISABLED;
			}else{
				pendant_mpg_status = MPG_STATUS_ENABLE_ONGOING;
			}
		}
	}else{
		button_action_delay_cnt_ch[MPG_BUT_DELAY_CH] = 0;
	}

	// The program will enter this if statement, if the system
	// is enabled and it's MPg functionality is turned on
	if(pendant_status && pendant_data.mpg){
		// Keep or "discard" axis movement data based on locks states
		if(lock_x_axis == GPIO_PIN_RESET){
			pendant_data.encoder1_val = ENCODER_1_TIM.Instance->CNT;
		}else{
			ENCODER_1_TIM.Instance->CNT = pendant_data.encoder1_val;
		}
		if(lock_yz_axis == GPIO_PIN_RESET){
			pendant_data.encoder2_val = ENCODER_2_TIM.Instance->CNT;
		}else{
			ENCODER_2_TIM.Instance->CNT = pendant_data.encoder2_val;
		}
	}else{
		// Discard encoder inputs
		pendant_data.encoder1_val = 0;
		pendant_data.encoder2_val = 0;
		ENCODER_1_TIM.Instance->CNT = 0;
		ENCODER_2_TIM.Instance->CNT = 0;
	}

	// If pendant's MPG functionality is enabled,
	// execute the following code inside the if statement
	if(pendant_mpg_status == MPG_STATUS_ENABLED){
		pendant_data.spindle_mode = get_spindle_mode(); // Get spindle mode
		pendant_data.jog_mode = 0;	//TODO: need to have an input for jogging mode switching
		pendant_data.x_axis_multiplicity = get_x_axis_multiplier(); // Get X axis multiplier
		pendant_data.yz_axis_multiplicity = get_yz_axis_multiplier(); // Get Y/Z axes multiplier

		// Check Y/Z axes switch input
		if(get_button_state(YZ_SW_CH) == GPIO_PIN_RESET){
			if(!y_or_z_last_state){
				y_or_z_last_state = true;
				button_action_delay_cnt_ch[Y_OR_Z_BUT_DELAY_CH] = 0;
			}
			if(++button_action_delay_cnt_ch[Y_OR_Z_BUT_DELAY_CH] >= button_delay_action_cnt){
				button_action_delay_cnt_ch[Y_OR_Z_BUT_DELAY_CH] = 0;
				pendant_data.y_or_z = YZ_MOVEMENT_Z;	// Set to Z axis
			}
		}else{
			if(y_or_z_last_state){
				y_or_z_last_state = false;
				button_action_delay_cnt_ch[Y_OR_Z_BUT_DELAY_CH] = 0;
			}
			if(++button_action_delay_cnt_ch[Y_OR_Z_BUT_DELAY_CH] >= button_delay_action_cnt){
				button_action_delay_cnt_ch[Y_OR_Z_BUT_DELAY_CH] = 0;
				pendant_data.y_or_z = YZ_MOVEMENT_Y;	// Set to Z axis
			}
		}

		// Check FLOOD coolant switch input
		if(get_button_state(FLOOD_SW_CH) == GPIO_PIN_RESET){
			if(++button_action_delay_cnt_ch[FLOOD_BUT_DELAY_CH] >= button_delay_action_cnt){
				button_action_delay_cnt_ch[FLOOD_BUT_DELAY_CH] = 0;
				pendant_data.flood = (pendant_data.flood ? false : true);
			}
		}else{
			button_action_delay_cnt_ch[FLOOD_BUT_DELAY_CH] = 0;
		}

		// Check MIST coolant switch input
		if(get_button_state(MIST_SW_CH) == GPIO_PIN_RESET){
			if(++button_action_delay_cnt_ch[MIST_BUT_DELAY_CH] >= button_delay_action_cnt){
				button_action_delay_cnt_ch[MIST_BUT_DELAY_CH] = 0;
				pendant_data.mist = (pendant_data.mist ? false : true);
			}
		}else{
			button_action_delay_cnt_ch[MIST_BUT_DELAY_CH] = 0;
		}

		// Check HOLD and Cycle start button input
		if(get_button_state(HOLD_BUT_CH) == GPIO_PIN_RESET){	// System HOLD status
			pendant_data.system_status = Hold;		// Set system status to Hold
		}else if(get_button_state(CYCLE_START_BUT_CH) == GPIO_PIN_RESET){	// System CYCLE START status
			pendant_data.system_status = Idle;		// Set system status to Idle
		}

		// Set MPG status LED
		HAL_GPIO_WritePin(MPG_ON_LED_GPIO_Port, MPG_ON_LED_Pin, LED_STATE_ON);

		// Set / Reset LED for which axis between Y and Z is selected
		if(pendant_data.y_or_z == YZ_MOVEMENT_Z){
			HAL_GPIO_WritePin(YZ_SW_LED_Y_GPIO_Port, YZ_SW_LED_Y_Pin, LED_STATE_OFF);
			HAL_GPIO_WritePin(YZ_SW_LED_Z_GPIO_Port, YZ_SW_LED_Z_Pin, LED_STATE_ON);
		}else if(pendant_data.y_or_z == YZ_MOVEMENT_Y){
			HAL_GPIO_WritePin(YZ_SW_LED_Y_GPIO_Port, YZ_SW_LED_Y_Pin, LED_STATE_ON);
			HAL_GPIO_WritePin(YZ_SW_LED_Z_GPIO_Port, YZ_SW_LED_Z_Pin, LED_STATE_OFF);
		}

		// Set / Reset flood coolant LED
		if(pendant_data.flood){
			HAL_GPIO_WritePin(FLOOD_LED_GPIO_Port, FLOOD_LED_Pin, LED_STATE_ON);
		}else{
			HAL_GPIO_WritePin(FLOOD_LED_GPIO_Port, FLOOD_LED_Pin, LED_STATE_OFF);
		}

		// Set / Reset mist coolant LED
		if(pendant_data.mist){
			HAL_GPIO_WritePin(MIST_LED_GPIO_Port, MIST_LED_Pin, LED_STATE_ON);
		}else{
			HAL_GPIO_WritePin(MIST_LED_GPIO_Port, MIST_LED_Pin, LED_STATE_OFF);
		}

		// Set / Reset X axis multiplier LEDs
		switch(pendant_data.x_axis_multiplicity){
			case 0:
				HAL_GPIO_WritePin(AXIS_X_MULTIPLIER_LED_1_GPIO_Port, AXIS_X_MULTIPLIER_LED_1_Pin, LED_STATE_ON);
				HAL_GPIO_WritePin(AXIS_X_MULTIPLIER_LED_2_GPIO_Port, AXIS_X_MULTIPLIER_LED_2_Pin, LED_STATE_OFF);
				HAL_GPIO_WritePin(AXIS_X_MULTIPLIER_LED_3_GPIO_Port, AXIS_X_MULTIPLIER_LED_3_Pin, LED_STATE_OFF);
				break;
			case 1:
				HAL_GPIO_WritePin(AXIS_X_MULTIPLIER_LED_1_GPIO_Port, AXIS_X_MULTIPLIER_LED_1_Pin, LED_STATE_OFF);
				HAL_GPIO_WritePin(AXIS_X_MULTIPLIER_LED_2_GPIO_Port, AXIS_X_MULTIPLIER_LED_2_Pin, LED_STATE_ON);
				HAL_GPIO_WritePin(AXIS_X_MULTIPLIER_LED_3_GPIO_Port, AXIS_X_MULTIPLIER_LED_3_Pin, LED_STATE_OFF);
				break;
			case 2:
				HAL_GPIO_WritePin(AXIS_X_MULTIPLIER_LED_1_GPIO_Port, AXIS_X_MULTIPLIER_LED_1_Pin, LED_STATE_OFF);
				HAL_GPIO_WritePin(AXIS_X_MULTIPLIER_LED_2_GPIO_Port, AXIS_X_MULTIPLIER_LED_2_Pin, LED_STATE_OFF);
				HAL_GPIO_WritePin(AXIS_X_MULTIPLIER_LED_3_GPIO_Port, AXIS_X_MULTIPLIER_LED_3_Pin, LED_STATE_ON);
				break;
			default:
				break;
		}

		// Set / Reset YZ axis multiplier LEDs
		switch(pendant_data.x_axis_multiplicity){
			case 0:
				HAL_GPIO_WritePin(AXIS_YZ_MULTIPLIER_LED_1_GPIO_Port, AXIS_YZ_MULTIPLIER_LED_1_Pin, LED_STATE_ON);
				HAL_GPIO_WritePin(AXIS_YZ_MULTIPLIER_LED_2_GPIO_Port, AXIS_YZ_MULTIPLIER_LED_2_Pin, LED_STATE_OFF);
				HAL_GPIO_WritePin(AXIS_YZ_MULTIPLIER_LED_3_GPIO_Port, AXIS_YZ_MULTIPLIER_LED_3_Pin, LED_STATE_OFF);
				break;
			case 1:
				HAL_GPIO_WritePin(AXIS_YZ_MULTIPLIER_LED_1_GPIO_Port, AXIS_YZ_MULTIPLIER_LED_1_Pin, LED_STATE_OFF);
				HAL_GPIO_WritePin(AXIS_YZ_MULTIPLIER_LED_2_GPIO_Port, AXIS_YZ_MULTIPLIER_LED_2_Pin, LED_STATE_ON);
				HAL_GPIO_WritePin(AXIS_YZ_MULTIPLIER_LED_3_GPIO_Port, AXIS_YZ_MULTIPLIER_LED_3_Pin, LED_STATE_OFF);
				break;
			case 2:
				HAL_GPIO_WritePin(AXIS_YZ_MULTIPLIER_LED_1_GPIO_Port, AXIS_YZ_MULTIPLIER_LED_1_Pin, LED_STATE_OFF);
				HAL_GPIO_WritePin(AXIS_YZ_MULTIPLIER_LED_2_GPIO_Port, AXIS_YZ_MULTIPLIER_LED_2_Pin, LED_STATE_OFF);
				HAL_GPIO_WritePin(AXIS_YZ_MULTIPLIER_LED_3_GPIO_Port, AXIS_YZ_MULTIPLIER_LED_3_Pin, LED_STATE_ON);
				break;
			default:
				break;
		}

		// Set / Reset spindle mode LEDs
		switch(pendant_data.spindle_mode){
			case SPINDLE_MODE_CW:
				HAL_GPIO_WritePin(SPINDLE_CW_LED_GPIO_Port, SPINDLE_CW_LED_Pin, LED_STATE_ON);
				HAL_GPIO_WritePin(SPINDLE_CCW_LED_GPIO_Port, SPINDLE_CCW_LED_Pin, LED_STATE_OFF);
				break;
			case SPINDLE_MODE_CCW:
				HAL_GPIO_WritePin(SPINDLE_CW_LED_GPIO_Port, SPINDLE_CW_LED_Pin, LED_STATE_OFF);
				HAL_GPIO_WritePin(SPINDLE_CCW_LED_GPIO_Port, SPINDLE_CCW_LED_Pin, LED_STATE_ON);
				break;
			case SPINDLE_MODE_OFF:
				HAL_GPIO_WritePin(SPINDLE_CW_LED_GPIO_Port, SPINDLE_CW_LED_Pin, LED_STATE_OFF);
				HAL_GPIO_WritePin(SPINDLE_CCW_LED_GPIO_Port, SPINDLE_CCW_LED_Pin, LED_STATE_OFF);
				break;
			default:
				break;
		}

		// Set / Reset machine status LEDs
		if(pendant_data.system_status == Idle){
			HAL_GPIO_WritePin(CYCLE_START_LED_GPIO_Port, CYCLE_START_LED_Pin, LED_STATE_ON);
			HAL_GPIO_WritePin(HOLD_LED_GPIO_Port, HOLD_LED_Pin, LED_STATE_OFF);
		}else if(pendant_data.system_status == Hold){
			HAL_GPIO_WritePin(CYCLE_START_LED_GPIO_Port, CYCLE_START_LED_Pin, LED_STATE_OFF);
			HAL_GPIO_WritePin(HOLD_LED_GPIO_Port, HOLD_LED_Pin, LED_STATE_ON);
		}
	}else if(pendant_mpg_status == MPG_STATUS_DISABLED){
		// Turn off system LEDs
		turn_off_leds();
	}
}

/**
  * @brief Analyze spindle mode switch input and return spindle mode
  */
uint8_t get_spindle_mode(void){
	uint8_t button_states = 0x00;

	button_states |= (~get_button_state(SPINDLE_3POS_SW_NC_1_CH)) & 0x01;
	button_states |= (((~get_button_state(SPINDLE_3POS_SW_NC_2_CH)) & 0x01) << 1);

	if(button_states == 0x03){
		return SPINDLE_MODE_OFF;
	}else if(button_states == 0x01){
		return SPINDLE_MODE_CW;
	}else if(button_states == 0x02){
		return SPINDLE_MODE_CCW;
	}

	return SPINDLE_MODE_OFF;
}

/**
  * @brief Analyze X axis multiplier selector input and return the selected multiplier
  */
uint8_t get_x_axis_multiplier(void){
	uint8_t button_states = 0x00;

	button_states |= (~get_button_state(AXIS_X_MULTIPLIER_SW_NC_1_CH)) & 0x01;
	button_states |= (((~get_button_state(AXIS_X_MULTIPLIER_SW_NC_2_CH)) & 0x01) << 1);

	if(button_states == 0x03){
		return 0;
	}else if(button_states == 0x01){
		return 1;
	}else if(button_states == 0x02){
		return 2;
	}

	return 0;
}

/**
  * @brief Analyze Y/Z axes multiplier selector input and return the selected multiplier
  */
uint8_t get_yz_axis_multiplier(void){
	uint8_t button_states = 0x00;

	button_states |= (~get_button_state(AXIS_YZ_MULTIPLIER_SW_NC_1_CH) & 0x01);
	button_states |= (((~get_button_state(AXIS_YZ_MULTIPLIER_SW_NC_2_CH)) & 0x01) << 1);

	if(button_states == 0x03){
		return 0;
	}else if(button_states == 0x01){
		return 1;
	}else if(button_states == 0x02){
		return 2;
	}

	return 0;
}

/* USER CODE END 4 */
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


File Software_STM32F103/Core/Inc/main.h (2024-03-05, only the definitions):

#define FLOOD_LED_Pin GPIO_PIN_13
#define FLOOD_LED_GPIO_Port GPIOC
#define MIST_LED_Pin GPIO_PIN_14
#define MIST_LED_GPIO_Port GPIOC
#define CYCLE_START_LED_Pin GPIO_PIN_15
#define CYCLE_START_LED_GPIO_Port GPIOC
#define SPINDLE_MODE_SW_NC_1_Pin GPIO_PIN_4
#define SPINDLE_MODE_SW_NC_1_GPIO_Port GPIOA
#define SPINDLE_MODE_SW_NC_2_Pin GPIO_PIN_5
#define SPINDLE_MODE_SW_NC_2_GPIO_Port GPIOA
#define AXIS_X_MULTIPLIER_SW_NC_1_Pin GPIO_PIN_0
#define AXIS_X_MULTIPLIER_SW_NC_1_GPIO_Port GPIOB
#define AXIS_X_MULTIPLIER_SW_NC_2_Pin GPIO_PIN_1
#define AXIS_X_MULTIPLIER_SW_NC_2_GPIO_Port GPIOB
#define AXIS_YZ_MULTIPLIER_SW_NC_1_Pin GPIO_PIN_2
#define AXIS_YZ_MULTIPLIER_SW_NC_1_GPIO_Port GPIOB
#define AXIS_YZ_MULTIPLIER_SW_NC_2_Pin GPIO_PIN_10
#define AXIS_YZ_MULTIPLIER_SW_NC_2_GPIO_Port GPIOB
#define YZ_SW_Pin GPIO_PIN_11
#define YZ_SW_GPIO_Port GPIOB
#define MPG_SW_Pin GPIO_PIN_12
#define MPG_SW_GPIO_Port GPIOB
#define HOLD_Pin GPIO_PIN_13
#define HOLD_GPIO_Port GPIOB
#define CYCLE_START_Pin GPIO_PIN_14
#define CYCLE_START_GPIO_Port GPIOB
#define FLOOD_Pin GPIO_PIN_15
#define FLOOD_GPIO_Port GPIOB
#define MIST_Pin GPIO_PIN_8
#define MIST_GPIO_Port GPIOA
#define MPG_ON_LED_Pin GPIO_PIN_9
#define MPG_ON_LED_GPIO_Port GPIOA
#define AXIS_X_MULTIPLIER_LED_1_Pin GPIO_PIN_10
#define AXIS_X_MULTIPLIER_LED_1_GPIO_Port GPIOA
#define AXIS_X_MULTIPLIER_LED_2_Pin GPIO_PIN_11
#define AXIS_X_MULTIPLIER_LED_2_GPIO_Port GPIOA
#define AXIS_X_MULTIPLIER_LED_3_Pin GPIO_PIN_12
#define AXIS_X_MULTIPLIER_LED_3_GPIO_Port GPIOA
#define LOCK_X_AXIS_SW_Pin GPIO_PIN_13
#define LOCK_X_AXIS_SW_GPIO_Port GPIOA
#define LOCK_YZ_AXIS_SW_Pin GPIO_PIN_14
#define LOCK_YZ_AXIS_SW_GPIO_Port GPIOA
#define AXIS_YZ_MULTIPLIER_LED_1_Pin GPIO_PIN_15
#define AXIS_YZ_MULTIPLIER_LED_1_GPIO_Port GPIOA
#define AXIS_YZ_MULTIPLIER_LED_2_Pin GPIO_PIN_3
#define AXIS_YZ_MULTIPLIER_LED_2_GPIO_Port GPIOB
#define AXIS_YZ_MULTIPLIER_LED_3_Pin GPIO_PIN_4
#define AXIS_YZ_MULTIPLIER_LED_3_GPIO_Port GPIOB
#define YZ_SW_LED_Y_Pin GPIO_PIN_5
#define YZ_SW_LED_Y_GPIO_Port GPIOB
#define YZ_SW_LED_Z_Pin GPIO_PIN_6
#define YZ_SW_LED_Z_GPIO_Port GPIOB
#define HOLD_LED_Pin GPIO_PIN_7
#define HOLD_LED_GPIO_Port GPIOB
#define SPINDLE_CW_LED_Pin GPIO_PIN_8
#define SPINDLE_CW_LED_GPIO_Port GPIOB
#define SPINDLE_CCW_LED_Pin GPIO_PIN_9
#define SPINDLE_CCW_LED_GPIO_Port GPIOB
#define SPINDLE_3POS_SW_NC_1_CH 0
#define SPINDLE_3POS_SW_NC_2_CH 1
#define AXIS_X_MULTIPLIER_SW_NC_1_CH 2
#define AXIS_X_MULTIPLIER_SW_NC_2_CH 3
#define AXIS_YZ_MULTIPLIER_SW_NC_1_CH 4
#define AXIS_YZ_MULTIPLIER_SW_NC_2_CH 5
#define YZ_SW_CH 6
#define MPG_BUT_CH 7
#define HOLD_BUT_CH 8
#define CYCLE_START_BUT_CH 9
#define FLOOD_SW_CH 10
#define MIST_SW_CH 11
#define LOCK_X_AXIS_SW_CH 12
#define LOCK_YZ_AXIS_SW_CH 13
#define BUTTON_DELAY_ACTION_TIME 200
#define TIM4_INT_TIME 10
#define PROCESS_INPUTS_DELAY 50
#define TIM4_INT_ENTRIES (PROCESS_INPUTS_DELAY / TIM4_INT_TIME)

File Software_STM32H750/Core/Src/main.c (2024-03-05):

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
/* Includes ------------------------------------------------------------------*/
#include "main.h"

/* USER CODE BEGIN Includes */
#include "r61529.h"
#include "fonts.h"
#include "ft5436.h"
#include "r61529_screen_menu.h"
#include "sound_fx.h"
#include "systick_timer.h"
#include "stm32h7xx_it.h"


/* USER CODE END Includes */


I2C_HandleTypeDef hi2c3;
DMA_HandleTypeDef hdma_i2c3_rx;
DMA_HandleTypeDef hdma_i2c3_tx;

TIM_HandleTypeDef htim1;
TIM_HandleTypeDef htim3;
TIM_HandleTypeDef htim4;

UART_HandleTypeDef huart4;
UART_HandleTypeDef huart2;
UART_HandleTypeDef huart3;
DMA_HandleTypeDef hdma_uart4_rx;
DMA_HandleTypeDef hdma_uart4_tx;
DMA_HandleTypeDef hdma_usart2_rx;
DMA_HandleTypeDef hdma_usart3_tx;

void SystemClock_Config(void);
void PeriphCommonClock_Config(void);
static void MX_GPIO_Init(void);
static void MX_DMA_Init(void);
static void MX_I2C3_Init(void);
static void MX_USART2_UART_Init(void);
static void MX_TIM3_Init(void);
static void MX_TIM4_Init(void);
static void MX_TIM1_Init(void);
static void MX_UART4_Init(void);
static void MX_USART3_UART_Init(void);
/* USER CODE BEGIN PFP */
void Init_interfaces();

/* USER CODE END PFP */

/**
  * @brief  The application entry point.
  * @retval int
  */
int main(void)
{
  /* MCU Configuration--------------------------------------------------------*/

  /* Reset of all peripherals, Initializes the Flash interface and the Systick. */
  HAL_Init();

  /* Configure the system clock */
  SystemClock_Config();

/* Configure the peripherals common clocks */
  PeriphCommonClock_Config();

  /* Initialize all configured peripherals */
  MX_GPIO_Init();
  MX_DMA_Init();
  MX_I2C3_Init();
  MX_USART2_UART_Init();
  MX_TIM3_Init();
  MX_TIM4_Init();
  MX_TIM1_Init();
  MX_UART4_Init();
  MX_USART3_UART_Init();
  /* USER CODE BEGIN 2 */
  // Initialize interfaces
  Init_interfaces();

  /* USER CODE END 2 */

  /* Infinite loop */
  /* USER CODE BEGIN WHILE */
  while(1){
	// Switch board LED state between 650ms
	if(wait_ms_ch(1, 650)){
		if(HAL_GPIO_ReadPin(Board_LED_GPIO_Port, Board_LED_Pin) == GPIO_PIN_RESET){
			HAL_GPIO_WritePin(Board_LED_GPIO_Port, Board_LED_Pin, GPIO_PIN_SET);
		}else{
			HAL_GPIO_WritePin(Board_LED_GPIO_Port, Board_LED_Pin, GPIO_PIN_RESET);
		}
	}

	// Call function, implementing the menu of the control panel
	r61529_screen_menu();
    /* USER CODE END WHILE */

    /* USER CODE BEGIN 3 */
  }
  /* USER CODE END 3 */
}

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
/* USER CODE BEGIN 4 */
/**
  * @brief Initialize interfaces
  */
void Init_interfaces(){
	// Start GRBL UART reception in DMA mode
	start_grbl_uart_reception();

	// Turn on screen back light
	HAL_TIM_PWM_Start(&htim3, TIM_CHANNEL_2);

	// Start up TIM1 (timer for button de-bouncer)
	HAL_TIM_Base_Start_IT(&htim1);

	// Enable buzzer
	enable_buzzer();

	// Initialize touch screen controller
	Init_FT5436();

	// Initialize screen controller
	Init_R61529();
	R61529_SetRotation(ROTATE_DEFAULT);

	// Loading phase
	HAL_GPIO_WritePin(Board_LED_GPIO_Port, Board_LED_Pin, GPIO_PIN_SET);
	HAL_GPIO_WritePin(USER_LED_A_GPIO_Port, USER_LED_A_Pin, GPIO_PIN_SET);
	HAL_GPIO_WritePin(USER_LED_B_GPIO_Port, USER_LED_B_Pin, GPIO_PIN_SET);
	HAL_GPIO_WritePin(USER_LED_C_GPIO_Port, USER_LED_C_Pin, GPIO_PIN_SET);
	HAL_GPIO_WritePin(USER_LED_D_GPIO_Port, USER_LED_D_Pin, GPIO_PIN_SET);

	draw_loading_screen();

	HAL_GPIO_WritePin(Board_LED_GPIO_Port, Board_LED_Pin, GPIO_PIN_RESET);
	HAL_GPIO_WritePin(USER_LED_A_GPIO_Port, USER_LED_A_Pin, GPIO_PIN_RESET);
	HAL_GPIO_WritePin(USER_LED_B_GPIO_Port, USER_LED_B_Pin, GPIO_PIN_RESET);
	HAL_GPIO_WritePin(USER_LED_C_GPIO_Port, USER_LED_C_Pin, GPIO_PIN_RESET);
	HAL_GPIO_WritePin(USER_LED_D_GPIO_Port, USER_LED_D_Pin, GPIO_PIN_RESET);
}

/* USER CODE END 4 */
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


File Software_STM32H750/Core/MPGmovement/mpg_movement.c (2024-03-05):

/*
 * mpg_movement.c
 *
 *  Created on: Feb 11, 2024
 *      Author: AvatarBg111
 */

/* Private includes ----------------------------------------------------------*/
#include <mpg_movement.h>
#include "mpg_pendant.h"
#include "../grblHALComm/parser.h"
#include "../grblHALComm/sender.h"
#include "systick_timer.h"
#include "stm32h7xx_it.h"


/* Private define ------------------------------------------------------------*/

/* Private typedef -----------------------------------------------------------*/

/* Private macro -------------------------------------------------------------*/

/* External variables --------------------------------------------------------*/
extern grbl_data_t grbl_data;
extern pendant_data_t pendant_data;
extern pendant_control_t pendant_control;

extern UART_HandleTypeDef huart3;
extern uint8_t uart3_tx_buf[100];


/* Private variables ---------------------------------------------------------*/
mpg_settings_t mpg_settings = {
	.x_axis_multiplicity = {X_AXIS_MULTIPLICITY_DEFAULT_PRECISE, X_AXIS_MULTIPLICITY_DEFAULT_NORMAL, X_AXIS_MULTIPLICITY_DEFAULT_COARSE},
	.yz_axis_multiplicity = {YZ_AXIS_MULTIPLICITY_DEFAULT_PRECISE, YZ_AXIS_MULTIPLICITY_DEFAULT_NORMAL, YZ_AXIS_MULTIPLICITY_DEFAULT_COARSE},
	.jog_speeds = {JOG_SPEED_DEFAULT_SLOW, JOG_SPEED_DEFAULT_NORMAL, JOG_SPEED_DEFAULT_FAST},
	.spindle_speed = SPINDLE_SPEED_DEFAULT,
	.spindle_mode = SPINDLE_MODE_OFF,
};
const double X_AXIS_MULTIPLICITY_DIFF[3] = {0.01, 0.1, 0.1};
const double YZ_AXIS_MULTIPLICITY_DIFF[3] = {0.01, 0.1, 0.1};
const double JOG_SPEED_DIFF[3] = {10, 50, 100};


/* Private function prototypes -----------------------------------------------*/
void pendant_data_to_action(pendant_action_t);
void process_pendant_data_to_action(void);


/* Private user code -----------------------------------------------*/
/**
  * @brief Delete a given sub-menu
  */
void pendant_data_to_action(pendant_action_t data){
	double x_multiplicity = mpg_settings.x_axis_multiplicity[data.x_axis_multiplicity];
	double yz_multiplicity = mpg_settings.yz_axis_multiplicity[data.yz_axis_multiplicity];
	double x_movement = data.encoder1_val_diff * x_multiplicity;
	double yz_movement = data.encoder2_val_diff * yz_multiplicity;
	char grbl_movement_str[50] = {0};
	char y_or_z = 0;
	uint8_t spindle_mode = 0;

	// Send movement packet
	if(x_movement != 0.000 || yz_movement != 0.000){
		if(data.y_or_z == YZ_MOVEMENT_Y){
			y_or_z = 'Y';
		}else{
			y_or_z = 'Z';
		}
		sprintf(grbl_movement_str, "$J=G91G21X%f%c%fF%d\n", x_movement, y_or_z, yz_movement, mpg_settings.jog_speeds[data.jog_mode]);
		grbl_send_packet((uint8_t*)grbl_movement_str, strlen(grbl_movement_str));
		memset(grbl_movement_str, 0, strlen(grbl_movement_str));
	}

	// Send spindle packet
	if(grbl_data.spindle.state.on && data.spindle_mode == SPINDLE_MODE_OFF){
		spindle_mode = 5;
	}else if(!grbl_data.spindle.state.on && data.spindle_mode == SPINDLE_MODE_CW){
		spindle_mode = 3;
	}else if(!grbl_data.spindle.state.on && data.spindle_mode == SPINDLE_MODE_CCW){
		spindle_mode = 4;
	}
	if(spindle_mode){
		sprintf(grbl_movement_str, "M%dS%d\n", spindle_mode, mpg_settings.spindle_speed);
		grbl_send_packet((uint8_t*)grbl_movement_str, strlen(grbl_movement_str));
		memset(grbl_movement_str, 0, strlen(grbl_movement_str));
	}

	// Set/Reset flood coolant
	grbl_movement_str[1] = '\n';
	if(data.flood != grbl_data.coolant.flood){
		grbl_movement_str[0] = CMD_OVERRIDE_COOLANT_FLOOD_TOGGLE;
		grbl_send_packet((uint8_t*)grbl_movement_str, 2);
	}
	if(data.mist != grbl_data.coolant.mist){
		grbl_movement_str[0] = CMD_OVERRIDE_COOLANT_MIST_TOGGLE;
		grbl_send_packet((uint8_t*)grbl_movement_str, 2);
	}
	grbl_movement_str[0] = 0;
	grbl_movement_str[1] = 0;

	// System status (HOLD, CYCLE_START) TODO
	if(pendant_data.system_status == Idle && grbl_data.grbl.state != Idle && \
	   grbl_data.grbl.state != Run && grbl_data.grbl.state != Jog){
		grbl_movement_str[0] = CMD_CYCLE_START;
		grbl_send_packet((uint8_t*)grbl_movement_str, 1);
	}else if(pendant_data.system_status == Hold && grbl_data.grbl.state != Hold && \
			 grbl_data.grbl.state != Alarm && grbl_data.grbl.state != Check && \
			 grbl_data.grbl.state != Door && grbl_data.grbl.state != Sleep){
		grbl_movement_str[0] = CMD_FEED_HOLD;
		grbl_send_packet((uint8_t*)grbl_movement_str, 1);
	}
	grbl_movement_str[0] = 0;
}

/**
  * @brief Process the received pendant data and do the
  * according actions (via sending messages to GRBL)
  */
void process_pendant_data_to_action(void){
	static pendant_data_t data = {0};
	pendant_data_t current_data;
	pendant_action_t action = {0};

	// Copy current pendant data into local structure
	memcpy(&current_data, &pendant_data, sizeof(pendant_data_t));

	// Encoder X
	if((current_data.encoder1_val > data.encoder1_val) && (current_data.encoder1_val - data.encoder1_val) < 300){
		action.encoder1_val_diff = current_data.encoder1_val - data.encoder1_val;
	}else if(current_data.encoder1_val > data.encoder1_val){
		action.encoder1_val_diff = -((0xFFFF - current_data.encoder1_val) + data.encoder1_val);
	}else if((current_data.encoder1_val < data.encoder1_val) && (data.encoder1_val - current_data.encoder1_val) < 300){
		action.encoder1_val_diff = current_data.encoder1_val - data.encoder1_val;
	}else if(current_data.encoder1_val < data.encoder1_val){
		action.encoder1_val_diff = -((0xFFFF - data.encoder1_val) + current_data.encoder1_val);
	}

	// Encoder YZ
	if((current_data.encoder2_val > data.encoder2_val) && (current_data.encoder2_val - data.encoder2_val) < 300){
		action.encoder2_val_diff = current_data.encoder2_val - data.encoder2_val;
	}else if(current_data.encoder2_val > data.encoder2_val){
		action.encoder2_val_diff = -((0xFFFF - current_data.encoder2_val) + data.encoder2_val);
	}else if((current_data.encoder2_val < data.encoder2_val) && (data.encoder2_val - current_data.encoder2_val) < 300){
		action.encoder2_val_diff = current_data.encoder2_val - data.encoder2_val;
	}else if(current_data.encoder2_val < data.encoder2_val){
		action.encoder2_val_diff = -((0xFFFF - data.encoder2_val) + current_data.encoder2_val);
	}

	// Copy the rest of the data
	action.x_axis_multiplicity = current_data.x_axis_multiplicity;
	action.yz_axis_multiplicity = current_data.yz_axis_multiplicity;
	action.y_or_z = current_data.y_or_z;
	action.spindle_mode = current_data.spindle_mode;
	action.jog_mode = pendant_control.jog_mode;	//current_data.jog_mode;
	action.system_status = current_data.system_status;
	action.flood = current_data.flood;
	action.mist = current_data.mist;
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

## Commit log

2023-11-16 Base commit
    [CNC_interfaces_board.PrjPcb, PCB1.PcbDoc, Sheet1.SchDoc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]
2023-12-18 Added a PCB project
    [CNC_interfaces_board.PrjPcb, PCB1.PcbDoc, Sheet1.SchDoc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]
2024-01-23 Uploading STM32H750 project base
2024-01-23 Changed configurations to CNC control unit project
    [config.h, grblHAL F401 Blackpill.cfg]
2024-01-24 Added screen brightness configuration functionality
    [CNC_control_panel_stm32h750 Release.cfg]
2024-01-26 Fixed easter egg submenu. Tried to do make a submenu for changing the volume of the buzzer, but to no avail (I might try to fix it in the future, but for now it's priority is last)
    [CNC_control_panel_stm32h750.ioc, main.c, main.h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]
2024-02-09 Added some reference manual and user manuals. Removed easter egg. Added minimal MPG manual mode functionality (Entering/Exiting MPG mode and moving X and Y axes). Bugs are to be fixed.
    [config.h, grblHAL F401 Blackpill.cfg]
2024-02-27 Added changes to the project of the pendant. Now it's program controls the LEDs based on the inputs from the buttons and switches
2024-03-05 Adding V1.0 Beta of the whole project to the repository
    [CNC_control_panel_stm32h750 Release.cfg, CNC_interfaces_board.PrjPcb, Sheet1.SchDoc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]

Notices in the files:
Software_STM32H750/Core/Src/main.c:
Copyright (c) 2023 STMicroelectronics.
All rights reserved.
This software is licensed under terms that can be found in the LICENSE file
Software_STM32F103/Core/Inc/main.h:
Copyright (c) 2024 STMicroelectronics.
